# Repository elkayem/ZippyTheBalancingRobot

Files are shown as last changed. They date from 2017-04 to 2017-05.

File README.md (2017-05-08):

# ZippyTheBalancingRobot

ZIPPY_VIDEO (https://www.youtube.com/watch?v=0io5SwitLzY) 

(Click on image above for link to YouTube video)

Zippy 2.0 is a 3D printed Arduino Nano based balancing robot with a custom PCB.  The original prototype version was put together on a breadboard with lots of jumper wires.  This is certainly a great way to get started.  The STMicroelectronics 8A motor drivers do not come in a convenient package for breadboarding, but ST does provide evaluation boards which work well with a prototype system.

The frame can be printed in multiple colors by pausing the print at the right height and switching filament.  The SketchUp 2017 file is included for design customization.  The frame is put together with a few dozen M3x10mm bolts and hex nuts, and four M3 standoffs for the PCB.  I printed the frame in PLA with a 0.2mm layer height and 40% infill.  See more information on the 3D printed frame on [Thingiverse](http://www.thingiverse.com/thing:2291516). 

I've also included an optional set of bumpers, which can protect Zippy in the event of a fall. Wrap the bumpers with pipe insulation tubes for a little extra cushion. Yes, the bumpers detract from Zippy's graceful physique, but make Zippy a little more rugged for kids.

The PCB yields a more compact design than a hand-soldered protoboard, but does require some SMD work and an additional outlay for PCB manufacture.  Even with the fine 0.5 mm pitch, the drivers can be hand soldered to the board (I did!) with a steady hand and patience.  There are plenty of YouTube videos on how to do this.

Here are the important parts for Zippy:
* 2 x VNH5180A motor drivers ($3.72 each as SMD parts, or $8.69 each as evaluation boards from Mouser)
* (Optional) Zippy printed circuit board (see Eagle files) $17.60 from EasyEDA or other PCB maufacturers
* 2 x 30:1 Metal Gearmotor 37Dx68L mm with 64 CPR Encoder ($39.95 each from Pololu)
* GY-521 MPU-6050 gyro/accelerometer breakout board ($4.78 from Amazon)
* Arduino Nano ($2.99 clone from Banggood)
* ZIPPY Flightmax 3000mAh 3S 20C LiPo battery ($22.49 from Amazon)
* 16x2 character LCD display ($5.99 from Amazon)
* Remote control with PWM receiver
* Two Schottky diodes (I used Fairchild SB1245 12A diodes, $1.57 each from Mouser)
* Various resistors, capacitors, 10K trimpot, pushbutton, connectors (see schematic)

I've also included a schematic in the Eagle folder.  Gerber files are provided in the Eagle folder if ordering from a PCB manufacturer.  Otherwise, use a breadboard and wire according to the enclosed schematic.

Pay close attention to polarity on motor wheels (swapping motor leads as necessary) and MPU-6050 orientation.  The software assumes the gyro/accelerometer is mounted with the +X axis facing the front of the robot.  

Depending on your robot inertia, the PID gains may need to be retuned.  Increase as needed to achieve crisp response without any oscillation.  

Also, if you like the colored eyes in [Zippy's video](https://www.youtube.com/watch?v=0io5SwitLzY), I've included the source code for that too.  You need another Arduino Nano or Pro Mini, two RGB LEDs (I used common anode), and six 300 ohm resistors.  The code shows which pins I used.  I just soldered the wires directly to the board, which is attached behind the face plate.  I can control the color, or have a changing rainbow pattern, using my remote control.  I used the left throttle stick on my RC remote.

Here are a few photos:

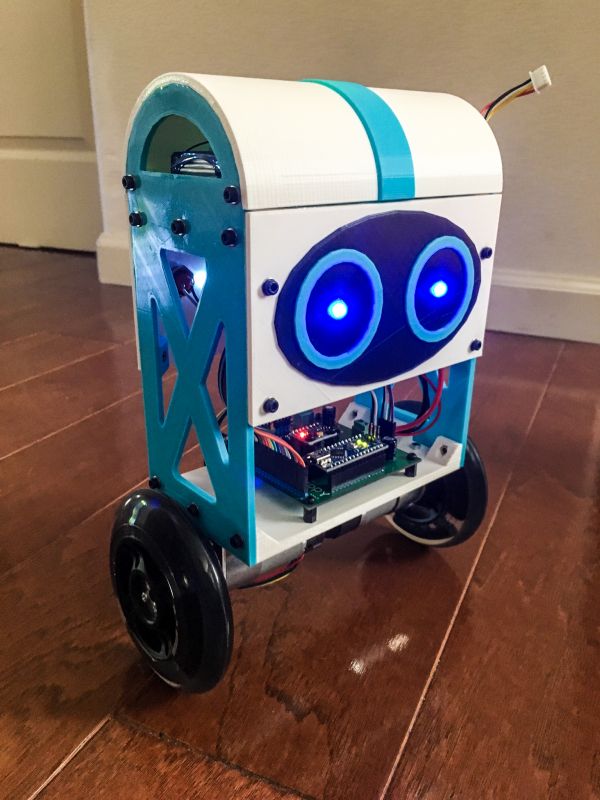
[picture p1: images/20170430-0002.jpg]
Zippy Front
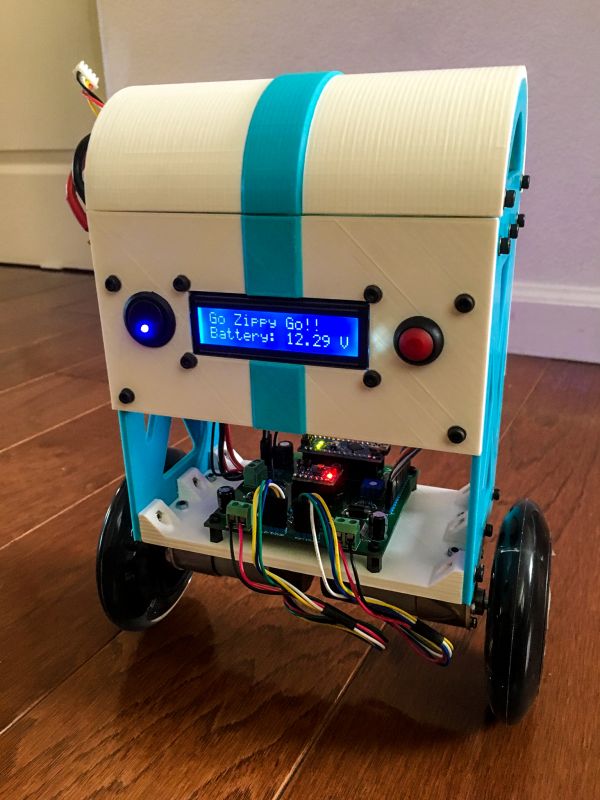
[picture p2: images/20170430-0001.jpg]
Zippy Back
  

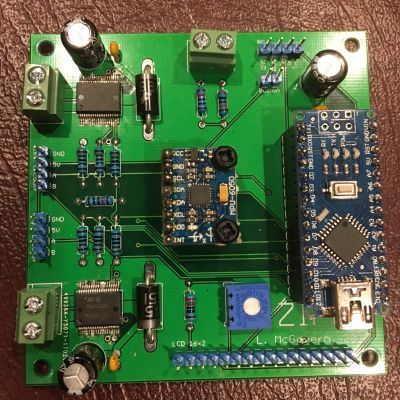
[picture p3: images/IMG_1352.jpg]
PCB
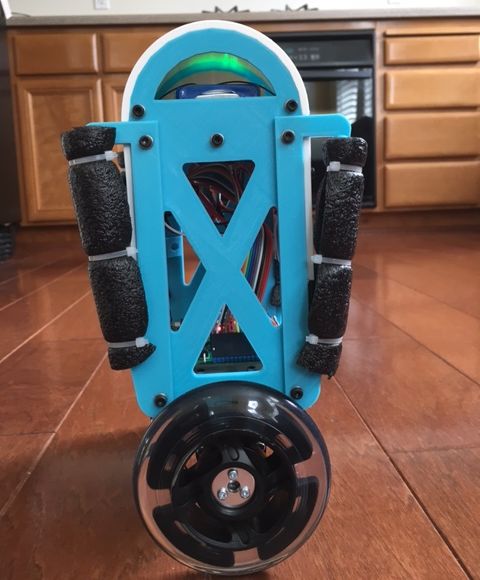
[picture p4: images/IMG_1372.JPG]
Bumpers
 

And a few photos of the prototype V1.0 version:

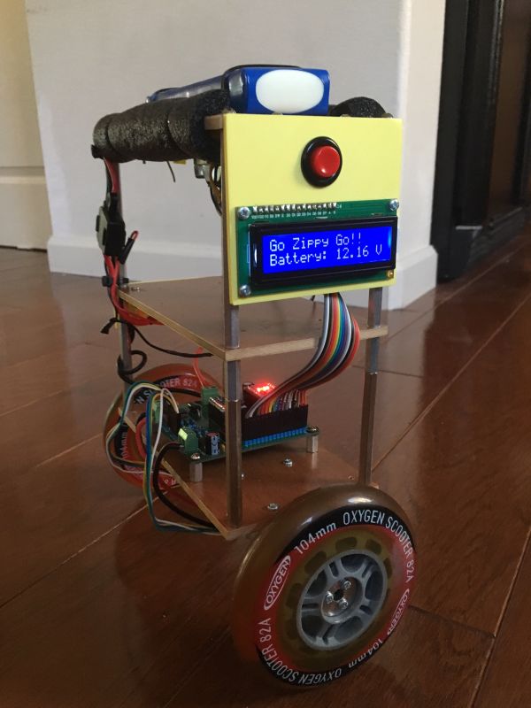
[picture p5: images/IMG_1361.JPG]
Zippy 1.0 Front
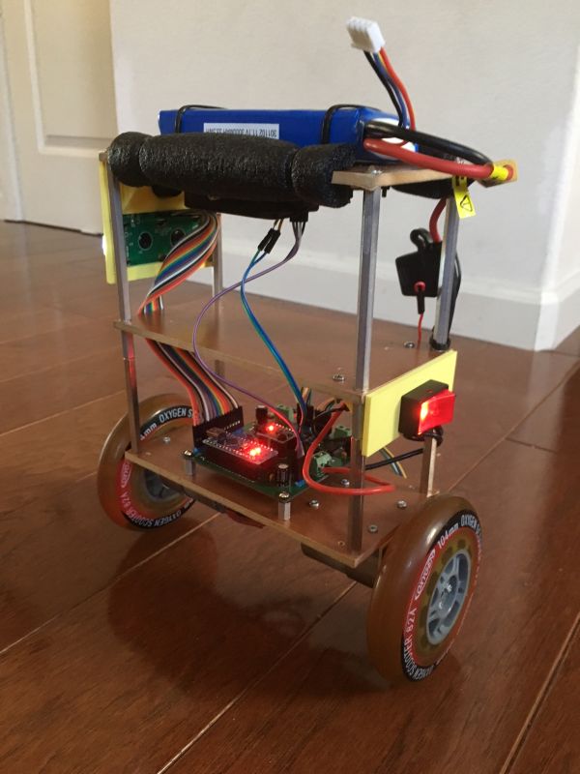
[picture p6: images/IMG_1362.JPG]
Zippy 1.0 Back


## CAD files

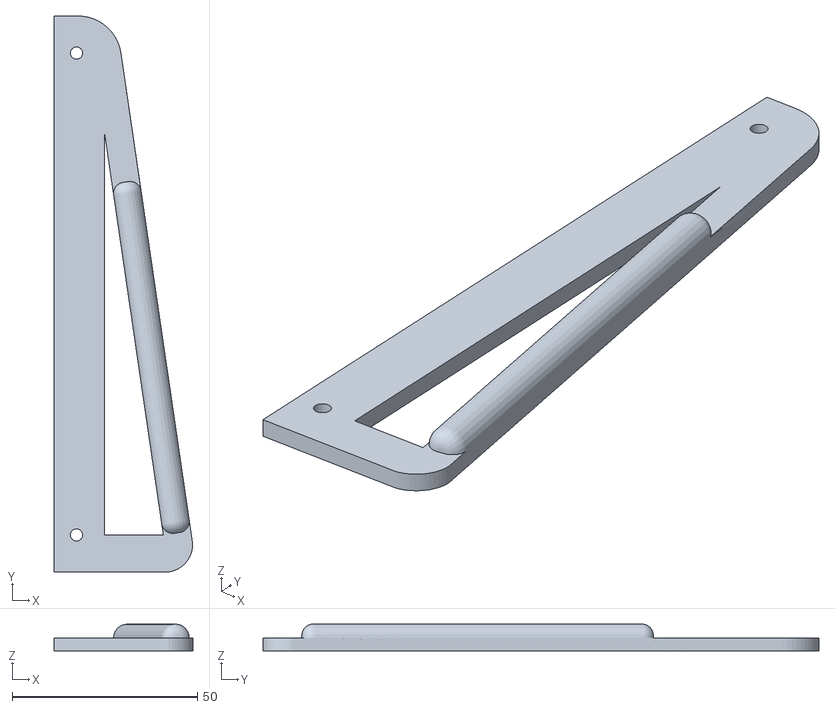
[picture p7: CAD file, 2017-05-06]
3D Printed Frame/LeftBumper.stl
37.4 x 150.0 x 7.25

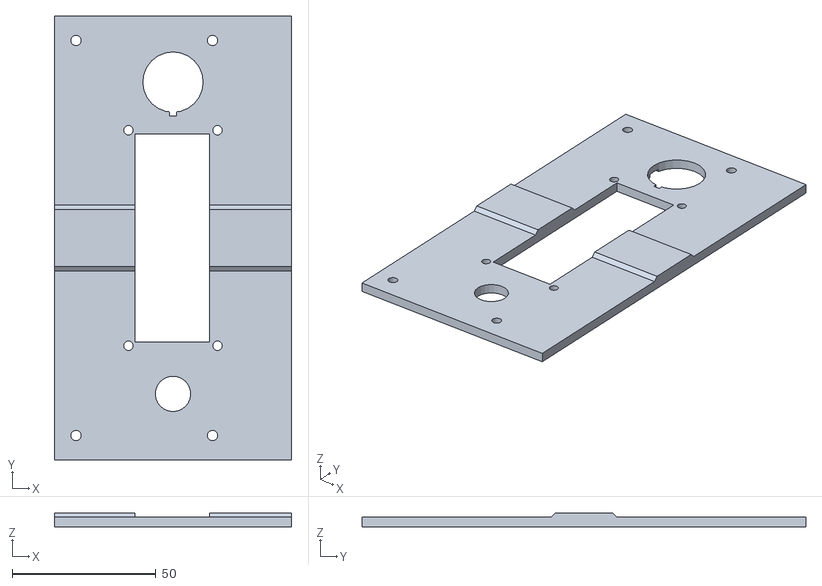
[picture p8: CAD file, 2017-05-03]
3D Printed Frame/ZippyBack.stl
82.5 x 154.5 x 5.00

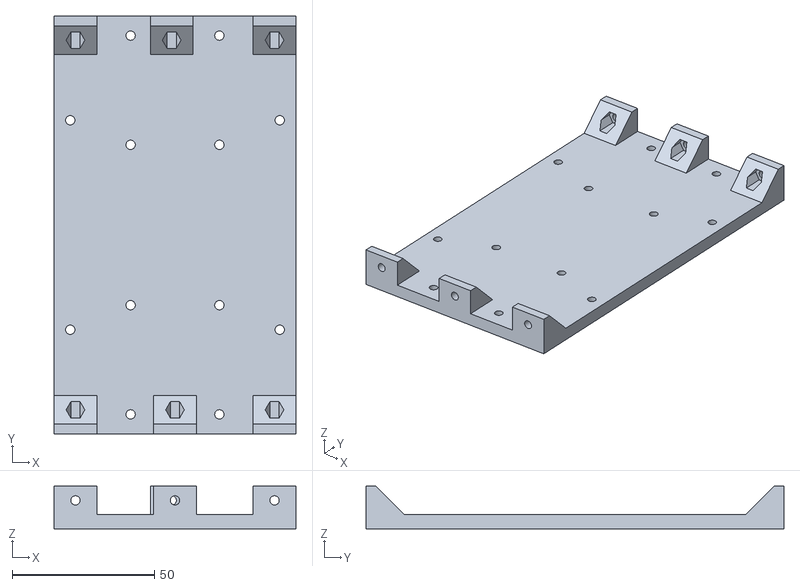
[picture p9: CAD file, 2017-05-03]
3D Printed Frame/ZippyMotorMount.stl
85.0 x 147.0 x 15.0

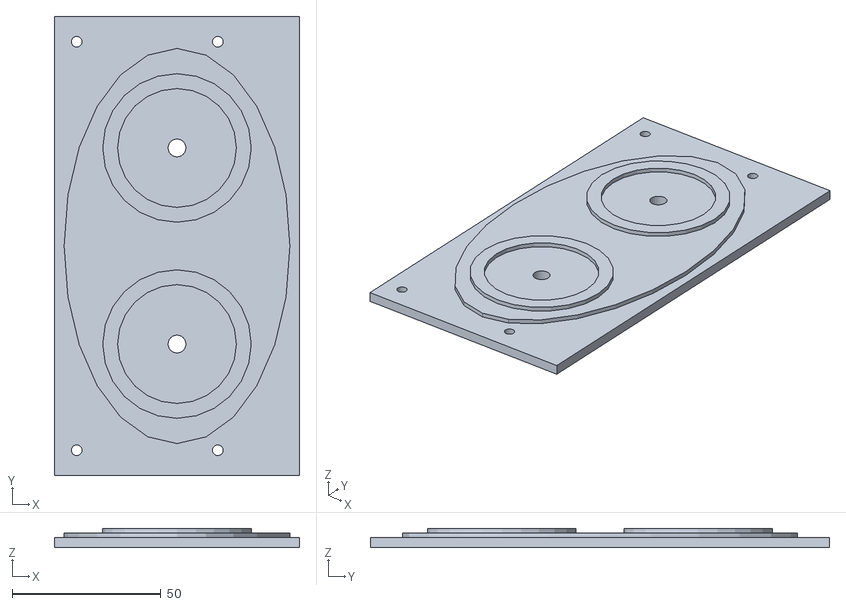
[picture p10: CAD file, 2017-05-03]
3D Printed Frame/ZippyFace.stl
82.5 x 154.5 x 6.50

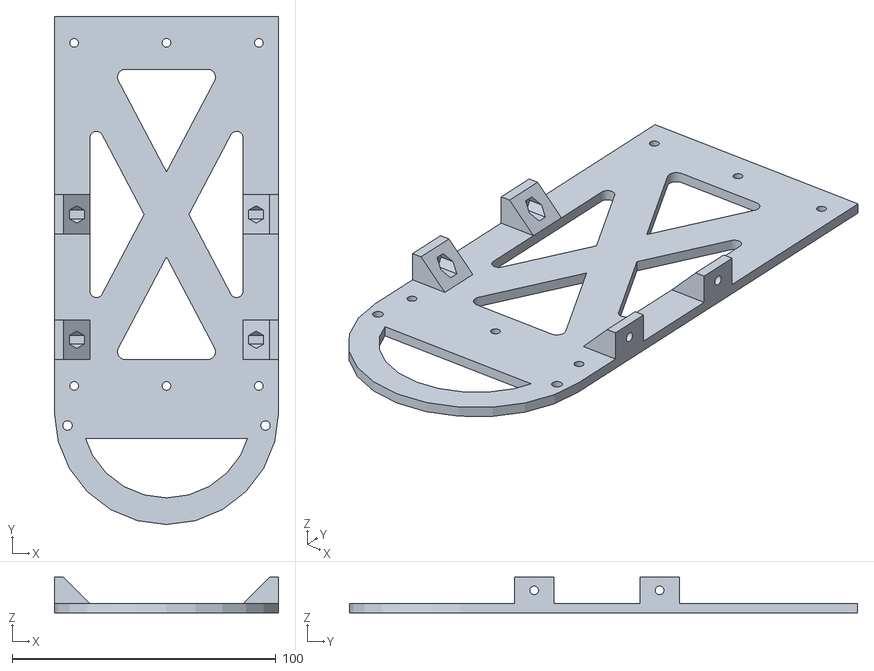
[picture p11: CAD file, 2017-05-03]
3D Printed Frame/ZippySide.stl
85.0 x 192.5 x 13.5

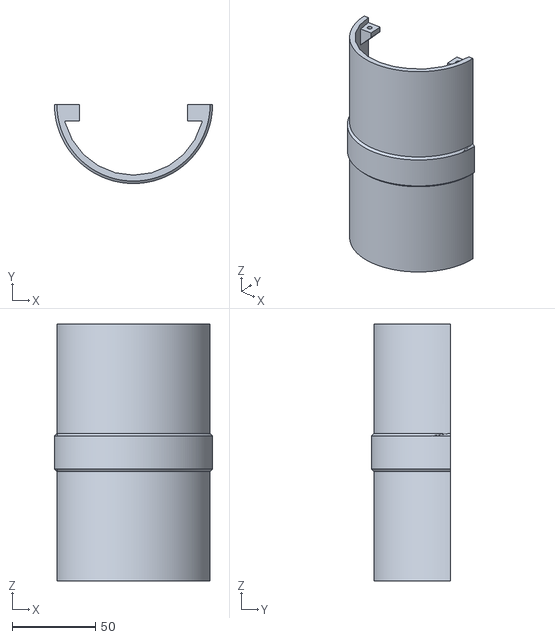
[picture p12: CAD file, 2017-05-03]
3D Printed Frame/ZippyLid.stl
95.1 x 47.5 x 154.5

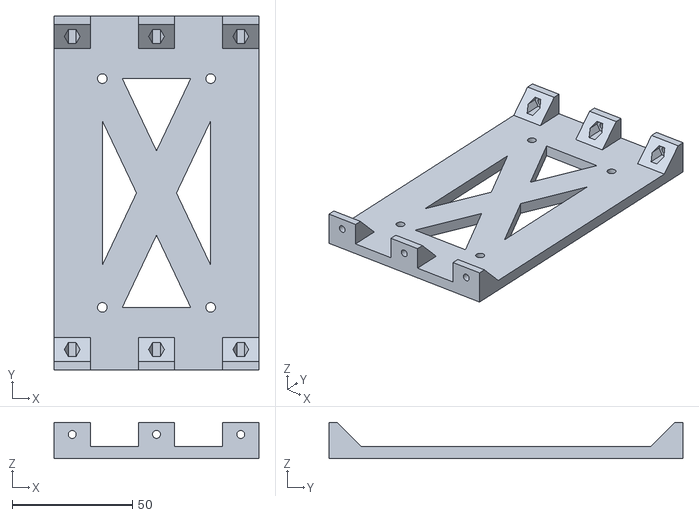
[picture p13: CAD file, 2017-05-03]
3D Printed Frame/ZippyTopPlate.stl
85.0 x 147.0 x 15.0

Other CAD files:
3D Printed Frame/RightBumper.stl
3D Printed Frame/Zippy.skp

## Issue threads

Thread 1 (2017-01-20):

Zippey Circuit diagram

BRoy98, 2017-01-20:
I just saw the video and Zippy is very stable and working awesome. I am planning to make one like this! Please provide a circuit diagram of Zippy also. So excited about this. Thanks in advance.

elkayem, 2017-01-21:
I'm glad you like the video and the design!  I wired it together on the fly, so never actually wrote down the schematic.  I get a lot of requests for the schematic, and so have been considering putting one together for quite some time.  Perhaps I'll even have a custom board manufactured for this!  I'll take your note as a challenge to put together a schematic.  I may not get around to it for a while (a few months?) but can definitely answer questions.

elkayem, 2017-01-23:
Ok, I finally broke down and put together a schematic in Eagle.  Look in the Eagle folder.  Closing this issue.

Closed 2017-01-23.

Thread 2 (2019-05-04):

No need to wait after Wire.requestFrom().

Koepel, 2019-05-04:
In the file "ZippyTheBalancingRobot.ino" in the function "i2cRead()" there is waiting after a Wire.requestFrom(), that waiting can be removed.
I have made an issue at Kristian's code repository in 2017: https://github.com/TKJElectronics/Balanduino/issues/3
Explanation: [Common-mistakes#1](https://github.com/Koepel/How-to-use-the-Arduino-Wire-library/wiki/Common-mistakes#1)

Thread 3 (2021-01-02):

clarification of the code

suibaf, 2021-01-02:
Hi,
I do not like to copy and paste the code, so I want to understand what you wrote. Copying and pasting is not enough, there are variables that if they are not respected, everything does not work: diameter of the wheels, distance between the wheels and more.
Your project is the best I see "around", but no one is able to reproduce it. I would like to try, but I needed some clarification.

- Can I use LCD in i2c bus? Why you use i2c only for MPU6050? for speed issues?
- In the code: what do you mean with VOLT_PER_COUNT 0.01465f ?
BR

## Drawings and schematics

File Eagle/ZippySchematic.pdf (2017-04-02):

# 5V 10K 5V GND

# 5V GND

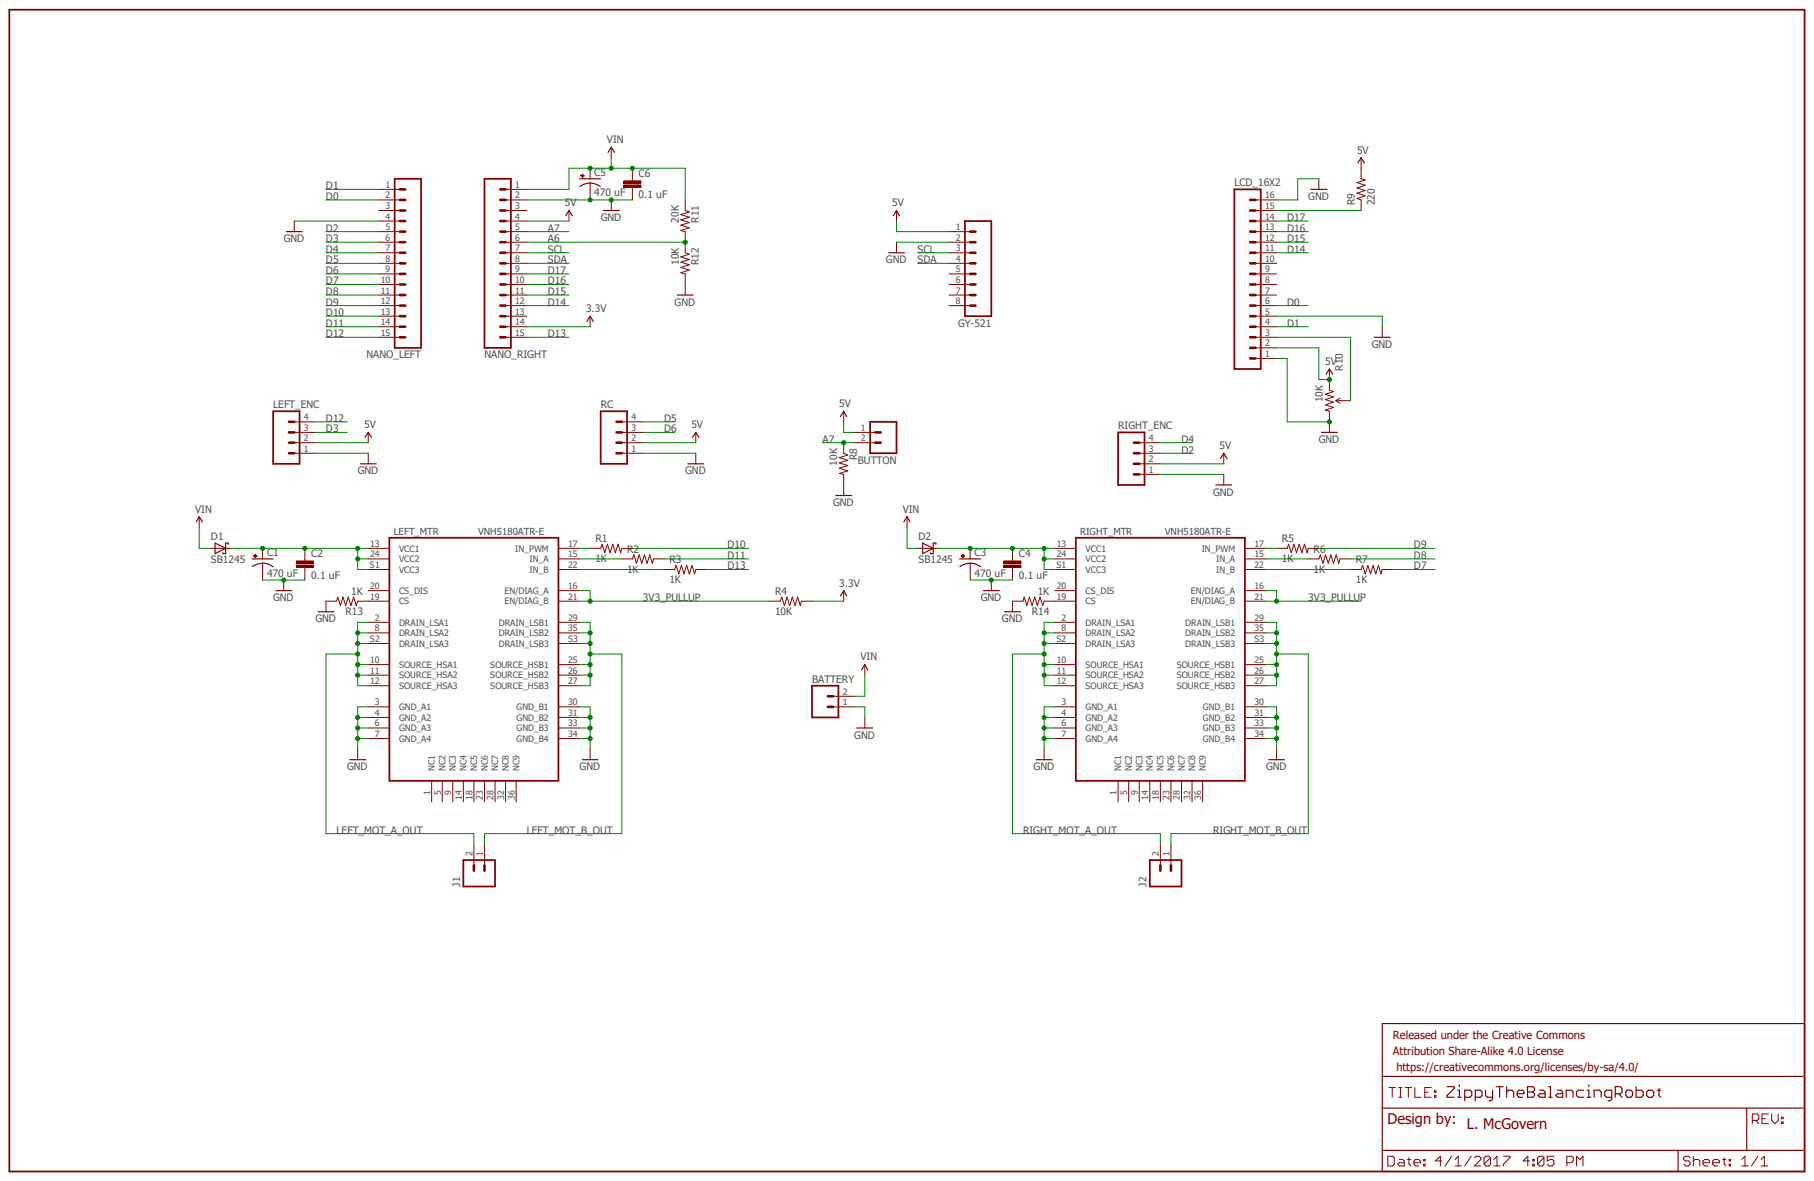
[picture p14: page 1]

L. McGovern Released under the Creative Commons Attribution Share-Alike 4.0 License

https://creativecommons.org/licenses/by-sa/4.0/ Design by:

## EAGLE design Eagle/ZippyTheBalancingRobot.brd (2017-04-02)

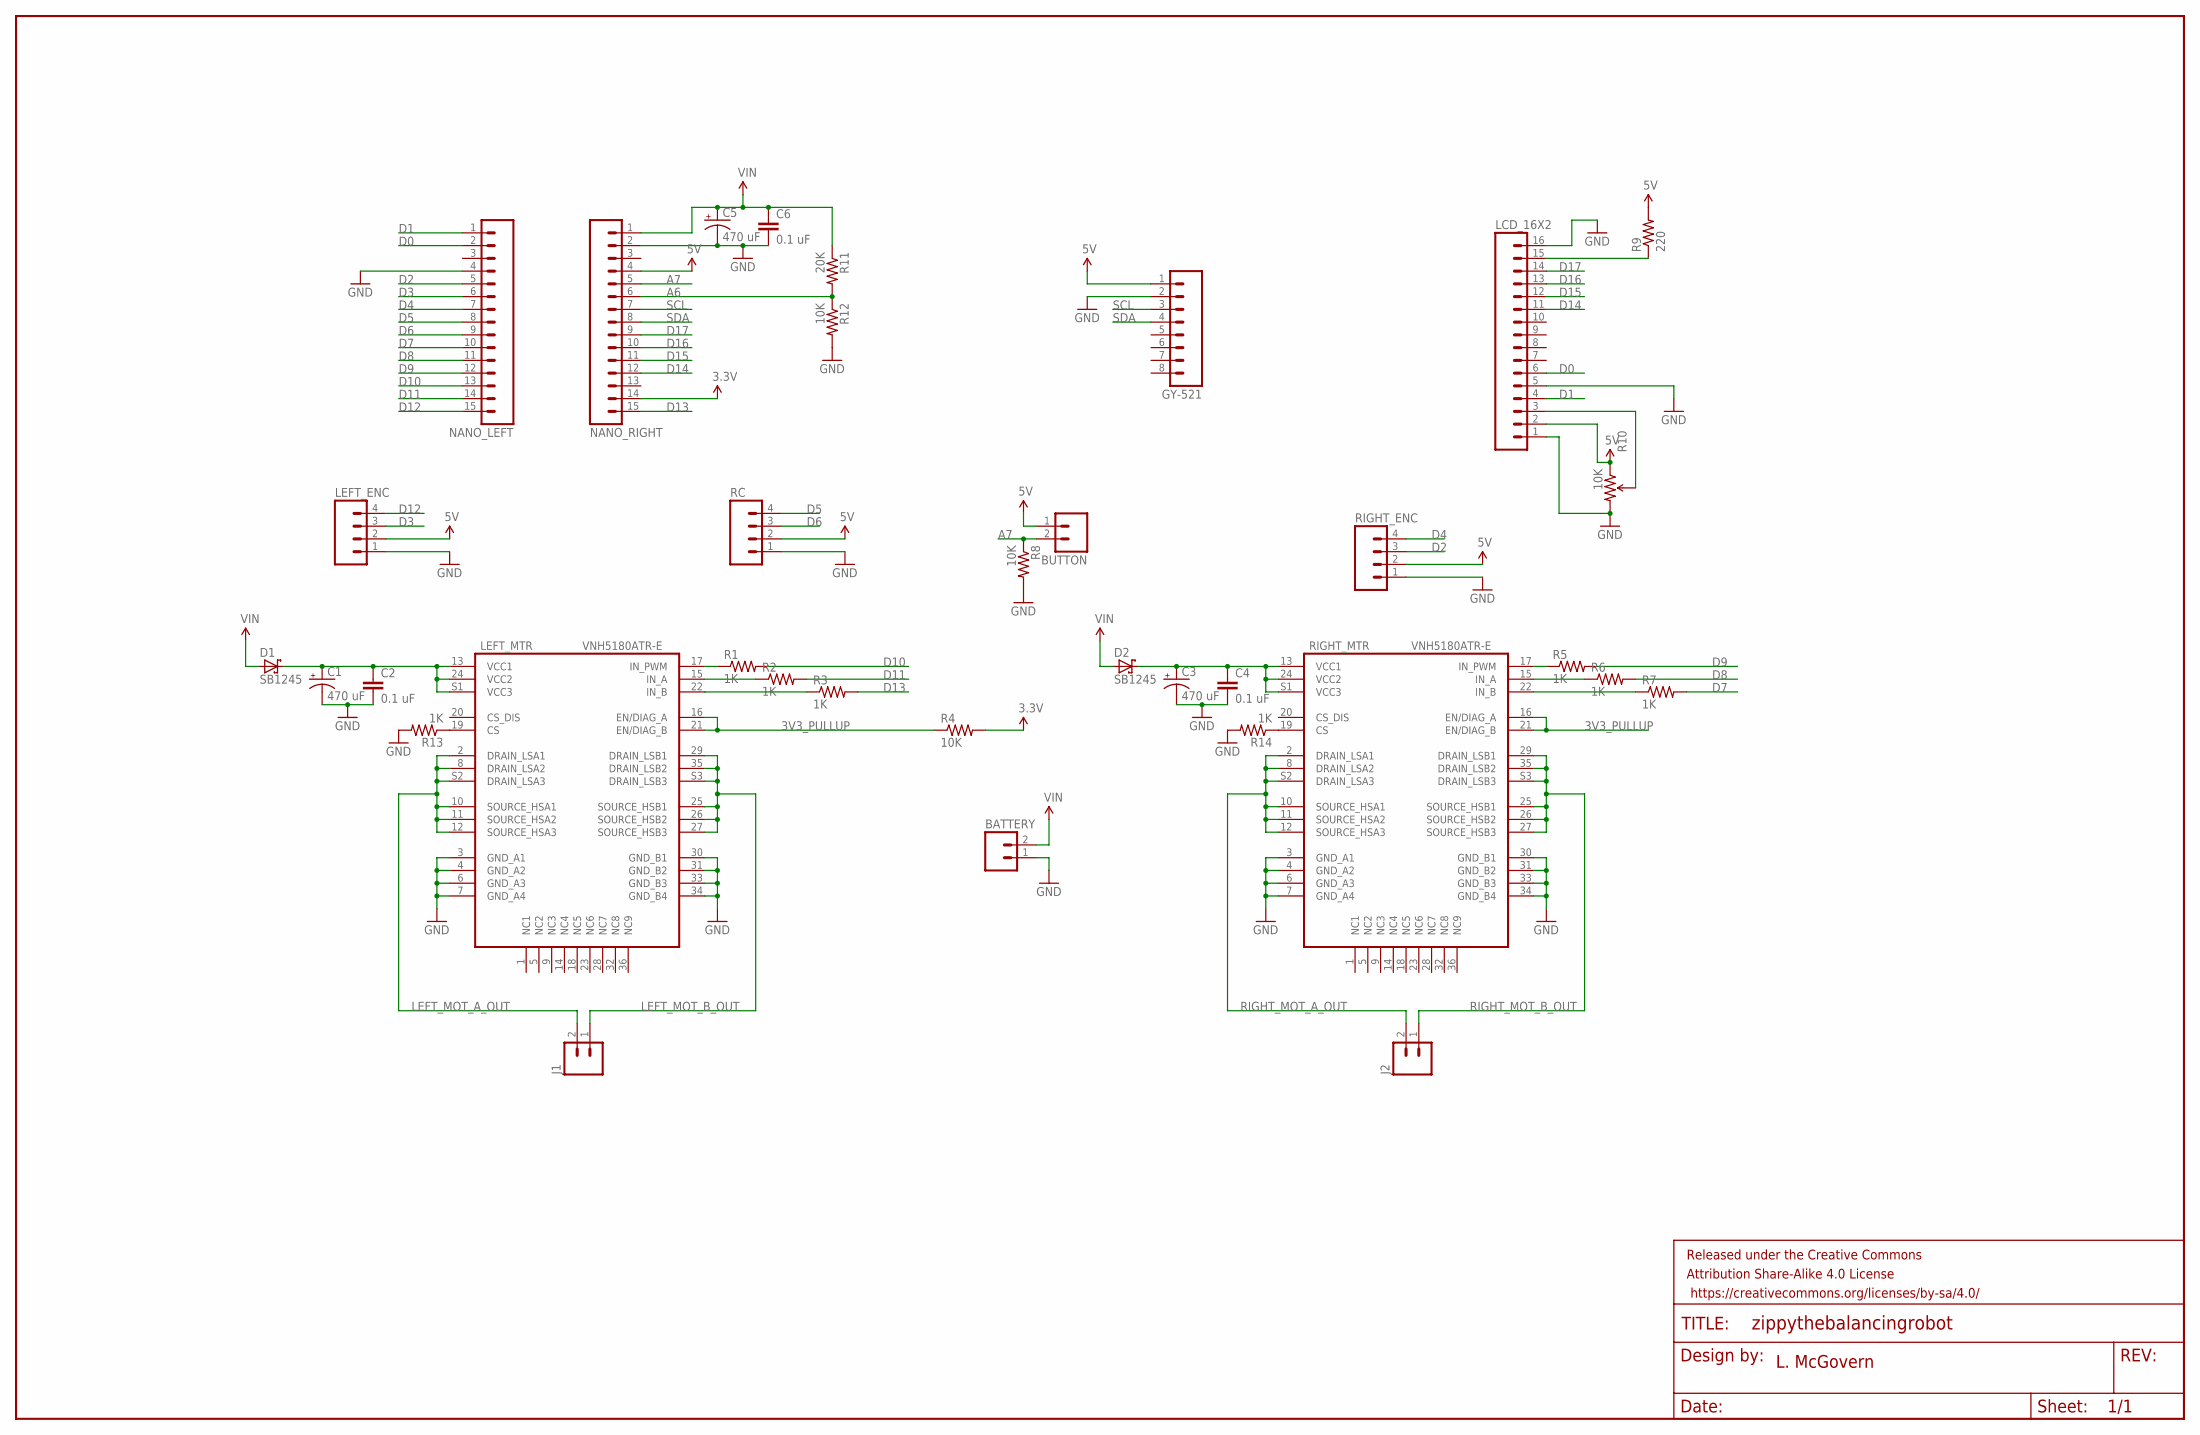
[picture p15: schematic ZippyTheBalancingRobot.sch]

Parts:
BATTERY: M025MM; SCREWTERMINAL-5MM-2
BUTTON: M02PTH; 1X02
C1, C3, C5: 470 uF; E3,5-8
C2, C4, C6: 0.1 uF; CAP-PTH-SMALL
D1, D2: SB1245; DO201T15
FRAME1: FRAME-LEDGER; CREATIVE_COMMONS
GY-521: M08; 1X08_ROUND
J1, J2: M025MM; SCREWTERMINAL-5MM-2
LCD_16X2: M16PTH; 1X16
LEFT_ENC: M04PTH; 1X04
LEFT_MTR: VNH5180ATR-E; POWERSSO-36
NANO_LEFT: M15; 1X15
NANO_RIGHT: M15; 1X15
R1, R2, R3, R5, R6, R7, R13, R14: 1K; 0207/10
R4, R8, R12: 10K; 0207/10
R9: 220; 0207/10
R10: 10K; 3386U
R11: 20K; 0207/10
RC: M04PTH; 1X04
RIGHT_ENC: M04PTH; 1X04
RIGHT_MTR: VNH5180ATR-E; POWERSSO-36

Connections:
3.3V: NANO_RIGHT.14, R4.2
3V3_PULLUP: LEFT_MTR.16 (EN/DIAG_A), LEFT_MTR.21 (EN/DIAG_B), R4.1, RIGHT_MTR.16 (EN/DIAG_A), RIGHT_MTR.21 (EN/DIAG_B)
5V: BUTTON.1, GY-521.1, LCD_16X2.2, LEFT_ENC.2, NANO_RIGHT.4, R9.2, R10.1 (CCW), RC.2, RIGHT_ENC.2
A6: NANO_RIGHT.6, R11.2, R12.1
A7: BUTTON.2, NANO_RIGHT.5, R8.1
D0: LCD_16X2.6, NANO_LEFT.2
D1: LCD_16X2.4, NANO_LEFT.1
D2: NANO_LEFT.5, RIGHT_ENC.3
D3: LEFT_ENC.3, NANO_LEFT.6
D4: NANO_LEFT.7, RIGHT_ENC.4
D5: NANO_LEFT.8, RC.4
D6: NANO_LEFT.9, RC.3
D7: NANO_LEFT.10, R7.2
D8: NANO_LEFT.11, R6.2
D9: NANO_LEFT.12, R5.2
D10: NANO_LEFT.13, R1.2
D11: NANO_LEFT.14, R2.2
D12: LEFT_ENC.4, NANO_LEFT.15
D13: NANO_RIGHT.15, R3.2
D14: LCD_16X2.11, NANO_RIGHT.12
D15: LCD_16X2.12, NANO_RIGHT.11
D16: LCD_16X2.13, NANO_RIGHT.10
D17: LCD_16X2.14, NANO_RIGHT.9
GND: BATTERY.1, C1.-, C2.2, C3.-, C4.2, C5.-, C6.2, GY-521.2, LCD_16X2.1, LCD_16X2.5, LCD_16X2.16, LEFT_ENC.1, LEFT_MTR.3 (GND_A1), LEFT_MTR.4 (GND_A2), LEFT_MTR.6 (GND_A3), LEFT_MTR.7 (GND_A4), LEFT_MTR.30 (GND_B1), LEFT_MTR.31 (GND_B2), LEFT_MTR.33 (GND_B3), LEFT_MTR.34 (GND_B4), NANO_LEFT.4, NANO_RIGHT.2, R8.2, R10.3 (CW), R12.2, R13.2, R14.2, RC.1, RIGHT_ENC.1, RIGHT_MTR.3 (GND_A1), RIGHT_MTR.4 (GND_A2), RIGHT_MTR.6 (GND_A3), RIGHT_MTR.7 (GND_A4), RIGHT_MTR.30 (GND_B1), RIGHT_MTR.31 (GND_B2), RIGHT_MTR.33 (GND_B3), RIGHT_MTR.34 (GND_B4)
LED+: LCD_16X2.15, R9.1
LEFT_MOT_A_OUT: J1.2, LEFT_MTR.2 (DRAIN_LSA1), LEFT_MTR.8 (DRAIN_LSA2), LEFT_MTR.10 (SOURCE_HSA1), LEFT_MTR.11 (SOURCE_HSA2), LEFT_MTR.12 (SOURCE_HSA3), LEFT_MTR.S2 (DRAIN_LSA3)
LEFT_MOT_B_OUT: J1.1, LEFT_MTR.25 (SOURCE_HSB1), LEFT_MTR.26 (SOURCE_HSB2), LEFT_MTR.27 (SOURCE_HSB3), LEFT_MTR.29 (DRAIN_LSB1), LEFT_MTR.35 (DRAIN_LSB2), LEFT_MTR.S3 (DRAIN_LSB3)
L_IN_A: LEFT_MTR.15 (IN_A), R2.1
L_IN_B: LEFT_MTR.22 (IN_B), R3.1
L_IN_PWM: LEFT_MTR.17 (IN_PWM), R1.1
unnamed: LEFT_MTR.19 (CS), R13.1
unnamed: R14.1, RIGHT_MTR.19 (CS)
unnamed: C1.+, C2.1, D1.C, LEFT_MTR.13 (VCC1), LEFT_MTR.24 (VCC2), LEFT_MTR.S1 (VCC3)
unnamed: C3.+, C4.1, D2.C, RIGHT_MTR.13 (VCC1), RIGHT_MTR.24 (VCC2), RIGHT_MTR.S1 (VCC3)
RIGHT_MOT_A_OUT: J2.2, RIGHT_MTR.2 (DRAIN_LSA1), RIGHT_MTR.8 (DRAIN_LSA2), RIGHT_MTR.10 (SOURCE_HSA1), RIGHT_MTR.11 (SOURCE_HSA2), RIGHT_MTR.12 (SOURCE_HSA3), RIGHT_MTR.S2 (DRAIN_LSA3)
RIGHT_MOT_B_OUT: J2.1, RIGHT_MTR.25 (SOURCE_HSB1), RIGHT_MTR.26 (SOURCE_HSB2), RIGHT_MTR.27 (SOURCE_HSB3), RIGHT_MTR.29 (DRAIN_LSB1), RIGHT_MTR.35 (DRAIN_LSB2), RIGHT_MTR.S3 (DRAIN_LSB3)
R_IN_A: R6.1, RIGHT_MTR.15 (IN_A)
R_IN_B: R7.1, RIGHT_MTR.22 (IN_B)
R_IN_PWM: R5.1, RIGHT_MTR.17 (IN_PWM)
SCL: GY-521.3, NANO_RIGHT.7
SDA: GY-521.4, NANO_RIGHT.8
V0: LCD_16X2.3, R10.2 (WIPER)
VIN: BATTERY.2, C5.+, C6.1, D1.A, D2.A, NANO_RIGHT.1, R11.1

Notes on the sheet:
L. McGovern

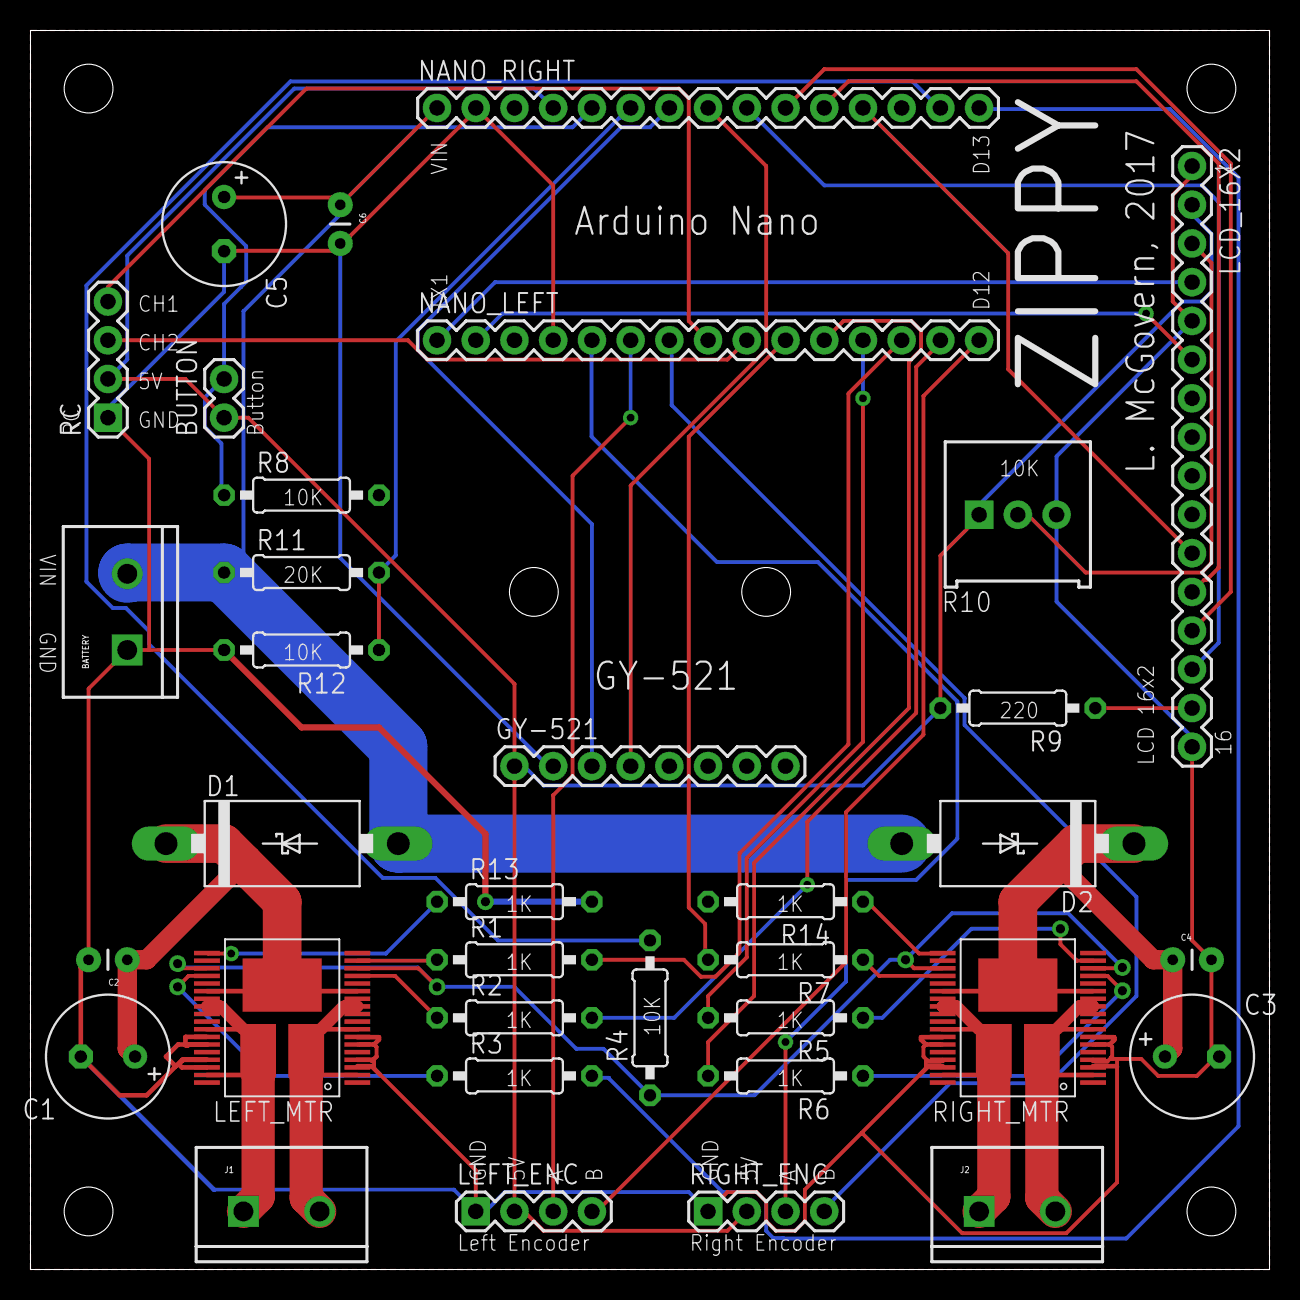
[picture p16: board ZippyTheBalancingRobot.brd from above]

Board: 2 copper layers, 81.3 x 81.3 mm, 36 parts (0 on the bottom side), 43 nets.

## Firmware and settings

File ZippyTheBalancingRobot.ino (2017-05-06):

/*
 * ZippyTheBalancingRobot -- Balancing Robot Control Software
 *
 *	  Copyright (C) 2015  Larry McGovern
 *
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
 *    Please also check out Kristian's code at https://github.com/TKJElectronics/Balanduino, which was a
 *    source of inspiration for this software
 */

#include <Wire.h>             // I2C Library
#include <PWM.h>              // PWM Frequency Library at https://code.google.com/archive/p/arduino-pwm-frequency-library/downloads
#include <EnableInterrupt.h>  // Enable Interrupt library
#include <digitalWriteFast.h> // DigitalWriteFast Library
#include <LiquidCrystal.h>    // Liquid Crystal library

// Uncomment CALCTIME to calculate processing time and display on LCD.  
// Time needs to be under 5 msec for reliable performance at 200 Hz

//#define CALCTIME  
/*
  LCD Circuit:
 * #1: LCD RS pin to digital pin 1
 * #2: LCD Enable pin to digital pin 0
 * #3: LCD D4 pin to digital pin 14
 * #4: LCD D5 pin to digital pin 15
 * #5: LCD D6 pin to digital pin 16
 * #6: LCD D7 pin to digital pin 17
 * LCD R/W pin to ground
 * LCD VSS pin to ground
 * LCD VCC pin to 5V
 * 10K resistor:
 * ends to +5V and ground
 * wiper to LCD VO pin (pin 3)
*/

// Pins

#define LCD_Pin1 1
#define LCD_Pin2 0
#define LCD_Pin3 14
#define LCD_Pin4 15
#define LCD_Pin5 16
#define LCD_Pin6 17

#define c_RightEncoderPinA 2
#define c_RightEncoderPinB 4

#define c_LeftEncoderPinA 3
#define c_LeftEncoderPinB 12

#define ThrottlePin 5
#define SteeringPin  6

#define MotorR_B 7
#define MotorR_A 8
#define MotorR_PWM 9

#define MotorL_PWM 10
#define MotorL_A 11
#define MotorL_B 13

#define buttonPin A7
#define voltSensePin A6

LiquidCrystal lcd(LCD_Pin1, LCD_Pin2, LCD_Pin3, LCD_Pin4, LCD_Pin5, LCD_Pin6);

volatile uint8_t bUpdateFlagsShared;
volatile uint16_t _ThrottleInShared;
volatile uint16_t _SteeringInShared;
uint32_t ThrottleStart;
uint32_t SteeringStart;

// Quadrature encoders
// Left encoder
#define LeftEncoderIsReversed
volatile bool _LeftEncoderBSet;
volatile long _LeftEncoderTicks = 0;

// Right encoder
volatile bool _RightEncoderBSet;
volatile long _RightEncoderTicks = 0;

#define DEG_PER_COUNT 0.75f      // 480 Counts per Revolution
#define VOLT_PER_COUNT 0.01465f  // 5 V * (30 kOhm)/(10 kOhm) / 1024

#define THROTTLE_FLAG 1
#define STEERING_FLAG 2
#define LEFTENC_FLAG 4
#define RIGHTENC_FLAG 8

#define DT 5000 // 5 msec time step
#define FHz 200 // Sample Rate

/*
 *  Control Gains
 */
#define PWMFREQ 10000
#define K_p 15.0f
#define K_i 100.0f
#define K_d 0.15f
#define wheelPosGain 0.0015f
#define wheelRateGain 0.003f
#define Kp_Rotation 0.1f
#define MaxAngleOffset 5.5f

uint32_t LastTime = 0;

float MotorScaleFactor = 0.01f;
bool RechargeBattery = 0;
 
// Gyro Address
static const uint8_t IMU = 0x68; // I2C address of the MPU-6050
uint8_t i2cBuffer[14];

float accAngle, gyroRate;
float PitchEst, BiasEst;

float gyroYzero;
float IntState = 0;  // Integral State

float voltageFilt = 0;

void setup(void)
{  
  lcd.begin(16, 2);
  lcd.print("Lay Zippy down");
  lcd.setCursor(0, 1);
  lcd.print("and press button");

  // Motor PWM Setup
  InitTimersSafe();  // Initialize timers for new PWM frequency
  SetPinFrequencySafe(MotorL_PWM, PWMFREQ);
  SetPinFrequencySafe(MotorR_PWM, PWMFREQ);

  // RC Receiver Setup
  pinMode(ThrottlePin, INPUT);
  digitalWrite(ThrottlePin, HIGH); //use the internal pullup resistor
  pinMode(SteeringPin, INPUT);
  digitalWrite(SteeringPin, HIGH); //use the internal pullup resistor
  
  enableInterrupt(ThrottlePin, calcThrottle, CHANGE);
  enableInterrupt(SteeringPin, calcSteering, CHANGE);
  
  // Quadrature encoder Setup
  // Left encoder
  pinMode(c_LeftEncoderPinA, INPUT);      // sets pin A as input
  digitalWrite(c_LeftEncoderPinA, LOW);  // turn on pulldown resistor
  pinMode(c_LeftEncoderPinB, INPUT);      // sets pin B as input
  digitalWrite(c_LeftEncoderPinB, LOW);  // pulldown resistor
  enableInterrupt(c_LeftEncoderPinA, HandleLeftMotorInterruptA, RISING);
  
  // Right encoder
  pinMode(c_RightEncoderPinA, INPUT);      // sets pin A as input
  digitalWrite(c_RightEncoderPinA, LOW);  // pulldown resistor
  pinMode(c_RightEncoderPinB, INPUT);      // sets pin B as input
  digitalWrite(c_RightEncoderPinB, LOW);  // pulldown resistor
  enableInterrupt(c_RightEncoderPinA, HandleRightMotorInterruptA, RISING);
  
  // Set up Gyro
  Wire.begin();
  Wire.setClock(400000UL); // Set I2C frequency to 400kHz

  while (i2cWrite(0x6B, 0x80, true)); // Reset device, this resets all internal registers to their default values
  do {
    while (i2cRead(0x6B, i2cBuffer, 1));
  } while (i2cBuffer[0] & 0x80); // Wait for the bit to clear
  delay(5);
  while (i2cWrite(0x6B, 0x09, true)); // PLL with X axis gyroscope reference, disable temperature sensor and disable sleep mode

  i2cBuffer[0] = 4; // Set the sample rate to 200Hz = 1kHz/(1+4)
  i2cBuffer[1] = 0x03; // Disable FSYNC and set 44 Hz Acc filtering, 42 Hz Gyro filtering, 1 KHz sampling
  i2cBuffer[2] = 0x00; // Set Gyro Full Scale Range to ±250deg/s
  i2cBuffer[3] = 0x00; // Set Accelerometer Full Scale Range to ±2g
  while (i2cWrite(0x19, i2cBuffer, 4, true)); // Write to all four registers at once
  delay(100); // Wait for the sensor to get ready

  /* Calibrate gyro zero value */
  
  while (analogRead(buttonPin) < 800);
  lcd.clear();
  lcd.print("Calibrating Gyro");
  
  while (calibrateGyro()); // Run again if the robot is moved while calibrating

  standUpRobot();  // Ask user to stand up robot and push button when ready

}

/*
 *  Main Loop
 */
void loop(void)
{
  int i;
  static unsigned long int timer, encoderTimer, voltageTimer, voltageTimerOut;
  static int throttle_glitch_persistent, steer_glitch_persistent;
  static float Error, wheelVelocity;
  static double wheelPosition, lastWheelPosition, rotationAngle;
  static unsigned long int WheelSpeedTimer;
  static double PosCmd, rotationCmd;
  static float AOCmd;
  static uint16_t ThrottleIn, SteeringIn, ThrottleInGood, SteeringInGood, bUpdateFlags;
  float ThrottleF, SteeringF;
  static long LeftEncoderTicks, RightEncoderTicks;
  float TorqueCMD;
  static float TurnTorque;
  int dutyCycle_L = 0, dutyCycle_R = 0;
  float AngleOffset;
  static unsigned long int CalcTime, MaxCalcTime, AveCalcTime, TimeCounter;
  static int NumSamples;

  // Turn off interrupts and copy over data which changes during interrupts
  if (bUpdateFlagsShared) {
    noInterrupts();
    bUpdateFlags = bUpdateFlagsShared;
    if (bUpdateFlags & THROTTLE_FLAG) {
      ThrottleIn = _ThrottleInShared;
    }
    if (bUpdateFlags & STEERING_FLAG)  {
      SteeringIn = _SteeringInShared;
    }
    if (bUpdateFlags & LEFTENC_FLAG) {
      LeftEncoderTicks = _LeftEncoderTicks;
    }
    if (bUpdateFlags & RIGHTENC_FLAG) {
      RightEncoderTicks = _RightEncoderTicks;
    }
    bUpdateFlagsShared = 0;
    interrupts(); // we have local copies of the inputs, so now we can turn interrupts back on
  }

  // Read and filter gyro data
  readIMUdata(&accAngle, &gyroRate);
  KalmanFilter(accAngle, gyroRate);

  // Calculate Wheel Position & Speed at 10 Hz
  if (millis() - WheelSpeedTimer > 100) {
    wheelPosition = 0.5f * (LeftEncoderTicks + RightEncoderTicks) * DEG_PER_COUNT;
    wheelVelocity = 10.0f * (wheelPosition - lastWheelPosition);
    rotationAngle = 0.5f * (LeftEncoderTicks - RightEncoderTicks) * DEG_PER_COUNT * 0.486f; // Rotation angle in deg.  Note: wheel diam = 104 mm
                                                                                            // and dist between wheels = 214 mm, so rotation 
                                                                                            // angle = 104 / 214 = 0.406 * wheel angle 
    lastWheelPosition = wheelPosition;
    WheelSpeedTimer = millis();
  }

  if (millis() - voltageTimer > 1000) {
    const float voltageFiltConst = 0.73; // K = exp(s*T), where s = 0.05*2*pi (1/20 Hz), and T = 1 sec
    float voltageFiltTemp = voltageFiltConst * voltageFilt + (1 - voltageFiltConst) * (float)analogRead(voltSensePin) * VOLT_PER_COUNT;
    if (!isnan(voltageFiltTemp)) {
      if (voltageFiltTemp > 9.5f && voltageFiltTemp < 13.0f) {
        voltageFilt = voltageFiltTemp;  // Update voltage only if measurement is within reasonable range
        MotorScaleFactor = 0.01f * 11.8f / voltageFilt;  // Adjust motor scale factor for ideal voltage of 11.8 V
      }
    }
    if (voltageFilt < 11.0f) {
      RechargeBattery = 1;
    }
    voltageTimer = millis();
  }
#ifndef CALCTIME
  if (millis() - voltageTimerOut > 10000) {
    lcd.clear();
    if (RechargeBattery) {
      lcd.print("Recharge Battery");
    }
    else {
      lcd.print("Go Zippy Go!!");
    }
    lcd.setCursor(0, 1);
    lcd.print("Battery: ");
    lcd.print(voltageFilt);
    lcd.print(" V");
    voltageTimerOut = millis();
  }
#endif

  if (PitchEst < -45 || PitchEst > 45) {  // Robot has fallen down

    // Disable motors
    digitalWriteFast(MotorL_A, LOW);  
    digitalWriteFast(MotorL_B, LOW);
    digitalWriteFast(MotorR_A, LOW);
    digitalWriteFast(MotorR_B, LOW);
    pwmWrite(MotorL_PWM, 0);
    pwmWrite(MotorR_PWM, 0);

    // Reset integrator and encoder position
    IntState = 0;
    _LeftEncoderTicks = 0; LeftEncoderTicks = 0;
    _RightEncoderTicks = 0; RightEncoderTicks = 0;

    wheelPosition = 0; lastWheelPosition = 0;
    wheelVelocity = 0; WheelSpeedTimer = millis();

    PosCmd = 0; rotationCmd = 0; 

    standUpRobot();  // Ask user to stand robot back up
    return;
  }
  else {
    
    // Filter ThrottleIn and convert to AOCmd
    if (ThrottleIn > 800 && ThrottleIn < 2200 && !RechargeBattery) {  // Valid range
      if ((abs(ThrottleIn - ThrottleInGood) < 200) || (throttle_glitch_persistent > 20)) { // Changes greater than 200 are assumed to be a glitch
        ThrottleInGood = ThrottleIn;
        throttle_glitch_persistent = 0;
      }
      else {
        throttle_glitch_persistent++;
      }
      ThrottleF = (float)ThrottleInGood;
      AOCmd = (ThrottleF - 1500.0f) / 75.0f; // SteeringIn ranges from 1000 to 2000.  Rescale to -6.7 to +6.7 deg
    }
    else {
      throttle_glitch_persistent++;
      if (throttle_glitch_persistent > 20) {
        throttle_glitch_persistent = 0;
      }
      AOCmd = 0;
    }
    AngleOffset = constrain(AOCmd, -MaxAngleOffset, MaxAngleOffset);  // Limits throttle input
    
    if (abs(AOCmd) > 1.0f) { // If angle offset command greater than 1 deg, then commanding forward/reverse motion
       PosCmd = wheelPosition + 1.0f * wheelVelocity;  // Set encoder position command to a location ahead of robot, 
                                                      // allowing robot to drift to a new location when stopping
       AngleOffset -=  wheelVelocity * wheelRateGain;
    }
    else { // Stop robot
      // Apply encoder feedback outer loop
      AngleOffset -= (wheelPosition - PosCmd) * wheelPosGain  + wheelVelocity * wheelRateGain;  // PD controller
    }
    AngleOffset = constrain(AngleOffset, -MaxAngleOffset, MaxAngleOffset);  // Additional limiter after outer loop
    
    Error = AngleOffset - PitchEst;
    IntState = IntState + Error / FHz;
    IntState = constrain(IntState, -5.0f, 5.0f);
    
    TorqueCMD = K_p * Error + K_i * IntState - K_d * gyroRate;  // PID Feedback Control

    // Filter SteeringIn and convert to TurnTorque
    if (SteeringIn > 800 && SteeringIn < 2200 && !RechargeBattery) {  // Valid range
      if ((abs(SteeringIn - SteeringInGood) < 200) || (steer_glitch_persistent > 20)) { // Changes greater than 200 are assumed to be a glitch
        SteeringInGood = SteeringIn;
        steer_glitch_persistent = 0;
      }
      else {
        steer_glitch_persistent++;
      }
      SteeringF = SteeringInGood;
      TurnTorque = (SteeringF - 1500.0f) / 20.0f;  // SteeringIn ranges from 1000 to 2000.  Rescale to -25 to 25.
      TurnTorque = constrain(TurnTorque, -25.0f, 25.0f);
      if (abs(TurnTorque) < 5.0f && abs(AOCmd) < 2.0f) {
        TurnTorque += Kp_Rotation * (rotationCmd - rotationAngle);  // Maintain current rotation angle
      }
      else {
        rotationCmd = rotationAngle;
      }
    }
    else {
      steer_glitch_persistent++;
      if (steer_glitch_persistent > 20) {
        steer_glitch_persistent = 0;
      }
      TurnTorque = 0;
    }

    dutyCycle_L = 255 * ((TorqueCMD - TurnTorque) * MotorScaleFactor);
    dutyCycle_R = 255 * ((TorqueCMD + TurnTorque) * MotorScaleFactor);

    if (dutyCycle_L < 0) {
      digitalWriteFast(MotorL_A, LOW);
      digitalWriteFast(MotorL_B, HIGH);
      dutyCycle_L = -dutyCycle_L;
    }
    else {
      digitalWriteFast(MotorL_A, HIGH);
      digitalWriteFast(MotorL_B, LOW);
    }

    if (dutyCycle_R < 0) {
      digitalWriteFast(MotorR_A, LOW);
      digitalWriteFast(MotorR_B, HIGH);
      dutyCycle_R = -dutyCycle_R;
    }
    else {
      digitalWriteFast(MotorR_A, HIGH);
      digitalWriteFast(MotorR_B, LOW);
    }
    if (dutyCycle_L > 255) {
      dutyCycle_L = 255;
    }
    if (dutyCycle_R > 255) {
      dutyCycle_R = 255;
    }
  }

  pwmWrite(MotorL_PWM, dutyCycle_L);
  pwmWrite(MotorR_PWM, dutyCycle_R);

#ifdef CALCTIME
  MaxCalcTime, AveCalcTime, TimeCounter, NumSamples;
  CalcTime = micros() - LastTime;
  if (MaxCalcTime < CalcTime) {
    MaxCalcTime = CalcTime;
  }
  AveCalcTime += CalcTime;
  NumSamples++;
  if ((millis() - TimeCounter) > 1000) {
    TimeCounter = millis();
    AveCalcTime /= NumSamples;
    NumSamples = 0;
    lcd.clear();
    lcd.print("Ave: ");
    lcd.print((float)AveCalcTime / 1000.0f);
    lcd.setCursor(0, 1);
    lcd.print("Max: ");
    lcd.print((float)MaxCalcTime / 1000.0f);
    MaxCalcTime = 0;
    AveCalcTime = 0;
  }
#endif

  while (micros() - LastTime < DT);
  LastTime = micros();
}

// Stand up robot and wait for button push
void standUpRobot() {
  lcd.clear();
  lcd.print("Stand & Push Btn");

  int button_pushed = 0;
  unsigned long timer;
  while (!button_pushed) {  // Calculate and display pitch until button pushed
    timer = millis();
    PitchEst = 0;
    for (int i = 0; i < 50; i++) {  // Average 50 samples
      readIMUdata(&accAngle, &gyroRate);
      PitchEst += accAngle;
      if (analogRead(buttonPin) > 800) {
        button_pushed = 1;
      }
    }
    PitchEst /= 50.0f;
    
    lcd.setCursor(0, 1);
    lcd.print("Pitch: ");
    lcd.print(PitchEst);
    while (millis() < timer + 250) {
      if (analogRead(buttonPin) > 800) {
        button_pushed = 1;
      }
    }
  }
  BiasEst = 0;
  
  for (int i = 0; i < 20; i++) {
    voltageFilt += (float)analogRead(voltSensePin) * VOLT_PER_COUNT;
  }
  voltageFilt /= 20.0f;

  lcd.clear();
  lcd.print("Go Zippy Go!!");
  lcd.setCursor(0, 1);
  lcd.print("Battery: ");
  lcd.print(voltageFilt);
  lcd.print(" V");
  delay(100);
  LastTime = micros();  
}

float KalmanFilter(float PitchMeas, float RateMeas) {
  /*
   * Steady State Kalman Filter -- Hard code gains into function
   *
   * [pitch; bias]_(k+1) = A * [pitch; bias]_(k) + B * rate_meas + G * w
   * pitch = C * [pitch; bias] + v
   *
   * A = [1 -dt; 0 1];
   * B = [dt; 0];
   * C = [1 0];
   *
   * G = [1 0; 0 1];
   * cov(w) = Q;
   * cov(v) = R;
   *
   * Kalman Filter gain solved using dlqe in Octave (GNU version of Matlab), assuming:
   * Q = diag([0.001 0.001]);
   * R = 1.5;
   * dt = 0.01;
   * then: K = dlqe(A,G,C,Q,R) = [0.033810; -0.025380];
   */
  const float dt = 0.005;
  const float K[2] = {0.016905, -0.012690}; // Gains originally calculated for 100 Hz,
  // Divide by 2 for 200 Hz gains
  float y = PitchMeas - PitchEst;
  PitchEst += dt * (RateMeas - BiasEst);
  PitchEst += K[0] * y;
  BiasEst  += K[1] * y;
}

bool calibrateGyro() {
  int16_t gyroYbuffer[50], AcX, AcZ;

  gyroYzero = 0;

  for (uint8_t i = 0; i < 50; i++) {
    readIMUdata(&accAngle, &gyroRate);
    gyroYbuffer[i] = gyroRate;
    gyroYzero += gyroYbuffer[i];
    delay(10);
  }
  if (!checkMinMax(gyroYbuffer, 50, 2000)) {  // Check that min and max differ by no more than 2000 counts (15 deg/sec)
                                              // Note: Zero-rate output spec value is +/- 20 deg/sec, so this value may
                                              // need to be increased for gyros with large drift
    return 1;
  }

  gyroYzero /= (50.0f * 131.0f);
  return 0;
}

bool checkMinMax(int16_t *array, uint8_t length, int16_t maxDifference) { // Used to check that the robot is laying still while calibrating
  int16_t min = array[0], max = array[0];
  for (uint8_t i = 1; i < length; i++) {
    if (array[i] < min)
      min = array[i];
    else if (array[i] > max)
      max = array[i];
  }
  return max - min < maxDifference;
}

/*
 * Interrupt services for RC Inputs (Throttle and Steering)
 */
void calcThrottle()
{
  // if the pin is high, its a rising edge of the signal pulse,
  // so lets record its value
  if (digitalReadFast(ThrottlePin) == HIGH)
  {
    ThrottleStart = micros();
  }
  else
  {
    // else it must be a falling edge, so lets get the time and subtract the time
    // of the rising edge this gives use the time between the rising and falling
    // edges i.e. the pulse duration.
    _ThrottleInShared = (uint16_t)(micros() - ThrottleStart);
  }
  // use set the throttle flag to indicate that a new throttle signal has been received
  bUpdateFlagsShared |= THROTTLE_FLAG;
}

void calcSteering()
{
  if (digitalReadFast(SteeringPin) == HIGH)
  {
    SteeringStart = micros();
  }
  else
  {
    _SteeringInShared = (uint16_t)(micros() - SteeringStart);
    bUpdateFlagsShared |= STEERING_FLAG;
  }
}

/*
 *  Interrupt service routines for the motor's quadrature encoder
 */
void HandleLeftMotorInterruptA()
{
  // Test transition; since the interrupt will only fire on 'rising' we don't need to read pin A
  _LeftEncoderBSet = digitalReadFast(c_LeftEncoderPinB);   // read the input pin

  // and adjust counter + if A leads B
#ifdef LeftEncoderIsReversed
  _LeftEncoderTicks -= _LeftEncoderBSet ? -1 : +1;
#else
  _LeftEncoderTicks += _LeftEncoderBSet ? -1 : +1;
#endif
  bUpdateFlagsShared |= LEFTENC_FLAG;
}

void HandleRightMotorInterruptA()
{
  // Test transition; since the interrupt will only fire on 'rising' we don't need to read pin A
  _RightEncoderBSet = digitalReadFast(c_RightEncoderPinB);   // read the input pin

  // and adjust counter + if A leads B
#ifdef RightEncoderIsReversed
  _RightEncoderTicks -= _RightEncoderBSet ? -1 : +1;
#else
  _RightEncoderTicks += _RightEncoderBSet ? -1 : +1;
#endif
  bUpdateFlagsShared |= RIGHTENC_FLAG;
}

void readIMUdata(float *accAngle, float *gyroRate) {
  while (i2cRead(0x3B, i2cBuffer, 14));
  int16_t AcX = ((i2cBuffer[0] << 8) | i2cBuffer[1]);
  int16_t AcZ = ((i2cBuffer[4] << 8) | i2cBuffer[5]);
  int16_t GyY = ((i2cBuffer[10] << 8) | i2cBuffer[11]);

  *accAngle = -atan2((float)AcX, (float)AcZ) * RAD_TO_DEG;
  *gyroRate = (float)GyY / 131.0f - gyroYzero; // Convert to deg/s
}

uint8_t i2cWrite(uint8_t registerAddress, uint8_t data, bool sendStop) {
  return i2cWrite(registerAddress, &data, 1, sendStop); // Returns 0 on success
}

uint8_t i2cWrite(uint8_t registerAddress, uint8_t *data, uint8_t length, bool sendStop) {
  Wire.beginTransmission(IMU);
  Wire.write(registerAddress);
  Wire.write(data, length);
  return(Wire.endTransmission(sendStop)); // Returns 0 on success
}

uint8_t i2cRead(uint8_t registerAddress, uint8_t *data, uint8_t nbytes) {
  uint32_t timeOutTimer;
  Wire.beginTransmission(IMU);
  Wire.write(registerAddress);
  uint8_t rcode = Wire.endTransmission(false); // Don't release the bus
  if (rcode) {
    return rcode; 
  }
  Wire.requestFrom(IMU, nbytes, (uint8_t)true); // Send a repeated start and then release the bus after reading
  for (uint8_t i = 0; i < nbytes; i++) {
    if (Wire.available())
      data[i] = Wire.read();
    else {
      timeOutTimer = micros();
      while (((micros() - timeOutTimer) < 100) && !Wire.available());
      if (Wire.available())
        data[i] = Wire.read();
      else {
        return 5; // Timeout
      }
    }
  }
  return 0; // Success
}

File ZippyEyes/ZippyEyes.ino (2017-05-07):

#include <digitalWriteFast.h> // DigitalWriteFast Library

#define RED_PIN 3
#define GREEN_PIN 5
#define BLUE_PIN 9

#define RC_PIN 2

enum colors {
  RED,
  GREEN,
  BLUE,
  RAINBOW
};
colors eyesMode = RAINBOW;

void setup() {
  pinMode(RC_PIN, INPUT_PULLUP);
  attachInterrupt(digitalPinToInterrupt(RC_PIN), calcRC, CHANGE); 
}

void loop() {
  static int rgb[3];
  static int dec = 0;
  static int counter = 0;

  switch(eyesMode) {
    case RED:
        writeRgb(255, 0, 0);
        break;
    case GREEN:
        writeRgb(0, 255, 0);
        break;        
     case BLUE:
        writeRgb(0, 0, 255);
        break; 
     case RAINBOW:
        if ((dec==0)&&(counter==0)) {
          rgb[0] = 255;
          rgb[1] = 0;
          rgb[2] = 0;         
        }
        writeRgb(rgb[0], rgb[1], rgb[2]);
        delay(25);
        
        int inc = (dec + 1) % 3;
        rgb[dec]--;
        rgb[inc]++;

        counter++;
        if (counter==255) {
          counter = 0;
          dec = (dec + 1) % 3;
        }
  }
}

void writeRgb(int red, int green, int blue) {
  analogWrite(RED_PIN, 255-red);  // Invert for common anode
  analogWrite(GREEN_PIN, 255-green);
  analogWrite(BLUE_PIN, 255-blue);
}

void calcRC()
{
  static unsigned int RC_Start;
  
  // if the pin is high, its a rising edge of the signal pulse,
  // so lets record its value
  if (digitalReadFast(RC_PIN) == HIGH)
  {
    RC_Start = micros();
  }
  else
  {
    // else it must be a falling edge, so lets get the time and subtract the time
    // of the rising edge this gives use the time between the rising and falling
    // edges i.e. the pulse duration.
    uint16_t RC_In = (uint16_t)(micros() - RC_Start);
    
    if (RC_In < 1250) {
      eyesMode = BLUE;
    } else if (RC_In < 1500) {
      eyesMode = RED;
    } else if (RC_In < 1750) {
      eyesMode = GREEN;
    } else {
      eyesMode = RAINBOW;
    }
  }
}

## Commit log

2017-01-23 Add schematic
    [ZippyTheBalancingRobot.sch]
2017-01-23 Update schematic
    [ZippyTheBalancingRobot.sch]
2017-01-26 Add board design
    [ZippyTheBalancingRobot.brd, ZippyTheBalancingRobot.sch]
2017-04-02 Update code for PCB, and fix PCB errors.
    [ZippyTheBalancingRobot.brd, ZippyTheBalancingRobot.sch]
2017-05-03 Add 3D printer files
    [Zippy.skp, ZippyBack.stl, ZippyFace.stl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]
2017-05-06 Tweak code for new frame
2017-05-06 Add bumpers
    [LeftBumper.stl, RightBumper.stl, Zippy.skp]

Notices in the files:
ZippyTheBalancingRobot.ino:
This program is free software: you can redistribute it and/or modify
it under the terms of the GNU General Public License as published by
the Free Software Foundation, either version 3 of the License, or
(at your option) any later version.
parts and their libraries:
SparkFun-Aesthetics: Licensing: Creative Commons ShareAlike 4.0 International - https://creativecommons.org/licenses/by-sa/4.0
